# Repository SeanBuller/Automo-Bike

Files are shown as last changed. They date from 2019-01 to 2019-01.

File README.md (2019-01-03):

## Automo-Bike

Automatic bicycle gear changer (transmission). Fourth year design project (Capstone) for ECE (Electrical & Computer Engineering) at University of Waterloo.

## Synopsis

Controls 2 stepper motors based on external inputs from hall-effect sensor, and IMU (inertial measurement unit). 12 V battery input with 5 V regulator for MCU. 

The design is intended to be paired with the following stepper motors: 17HS13-0404S-PG27 and SY20STH30-0604A.

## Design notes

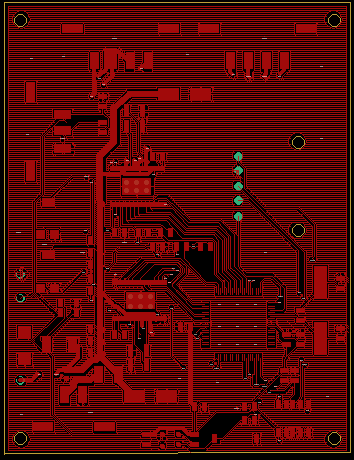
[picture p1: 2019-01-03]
FYDP-Schematic.GTL.png

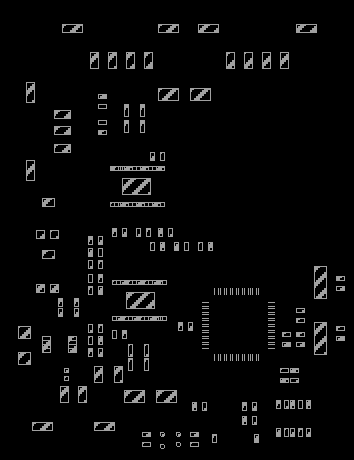
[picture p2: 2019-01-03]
FYDP-Schematic.GTP.png

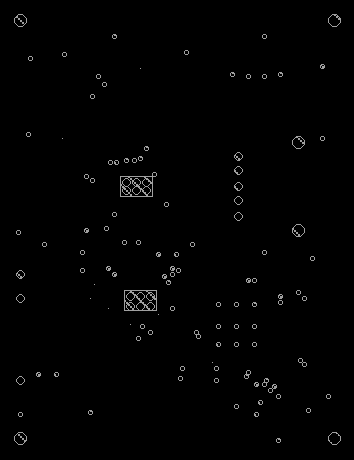
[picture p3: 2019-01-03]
FYDP-Schematic.GBS.png

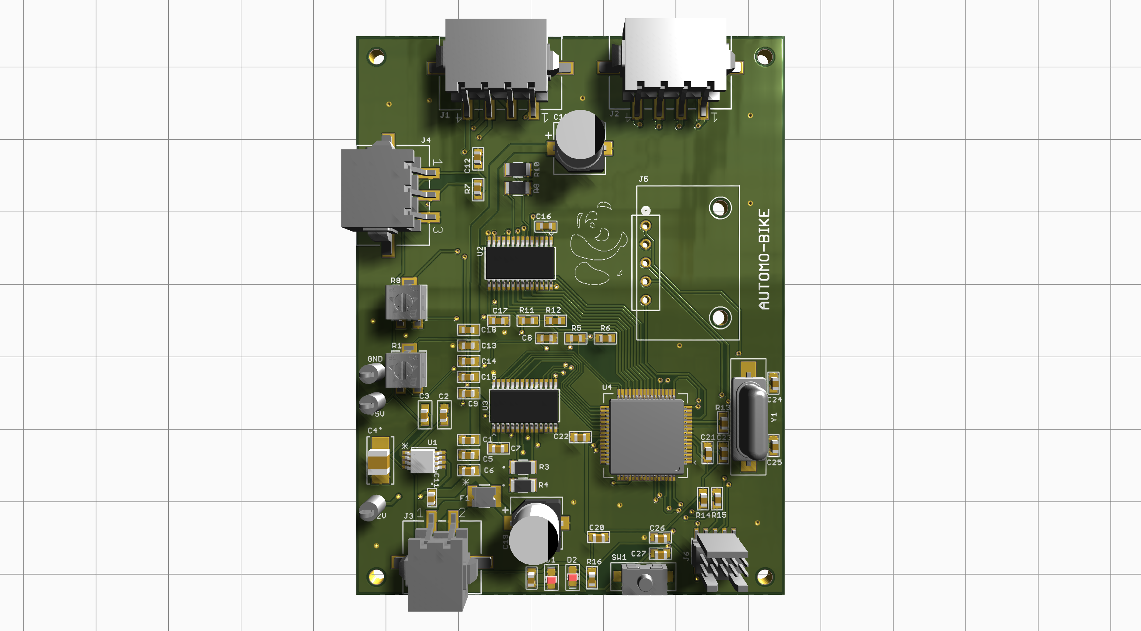
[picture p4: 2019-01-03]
FYDP-Schematic.brd.png

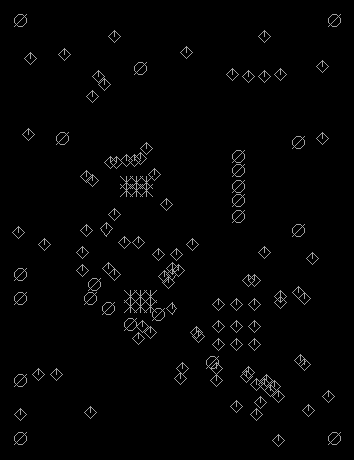
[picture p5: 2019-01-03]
FYDP-Schematic.TXT.png

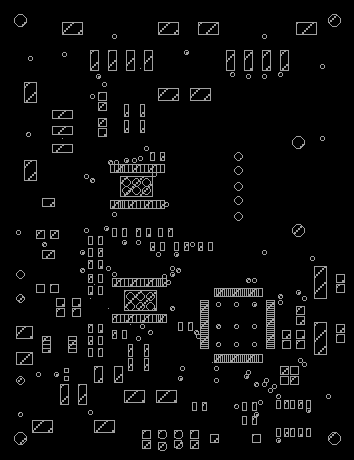
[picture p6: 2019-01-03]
FYDP-Schematic.GTS.png

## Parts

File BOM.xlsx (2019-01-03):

Qty | Value | Device | Package | Parts | Digikey Part # | Unit Price | Per Board Price
11 | 0.1 uF | C_0603 | 603 | C21, C22, C26, C27, C5, C6, C9, C12, C14, C15, C18 | 399-6856-1-ND | $0.13 | $0.82
2 | 0.47uF | C_0603 | 603 | C8, C17 | 490-3295-1-ND | $0.23 | $0.46
2 | 1.0uF | 1.0UF-0603-16V-10% | 603 | C2, C3 | 587-1251-1-ND | $0.13 | $0.26
4 | 1.5K | R_0603 | 603 | R5, R6, R11, R12 | RNCP0603FTD1K50CT-ND | $0.14 | $0.56
2 | 10K | R_0603 | 603 | R14, R15 | RR08P10.0KDCT-ND | $0.16 | $0.32
2 | 10nF | C_0603 | 603 | C7, C16 | 399-1091-1-ND | $0.13 | $0.26
1 | 10uF | F931C106MBA | F93-C | C4 | 478-8238-1-ND | $0.68 | $0.68
1 | 10uF | GRM188C81C106MA73D | G-188 | C11 | 490-7198-1-ND | $0.51 | $0.51
1 | 1210L110/12WR | 1210L110/12WR | 1210LSERIES | F1 | F6132CT-ND | $1.33 | $1.33
2 | 12pF | C_0603 | 603 | C24, C25 | 1276-1254-1-ND | $0.13 | $0.26
1 | 16 MHz | AT-16.000MAGE-T | AT-16.000MAGE-T | Y1 | 887-1608-1-ND | $0.94 | $0.94
3 | 1K | R_0603 | 603 | R2, R7, R16 | RR08P1.0KDCT-ND | $0.16 | $0.48
1 | 1M | R_0603 | 603 | R13 | A119955CT-ND | $0.74 | $0.74
2 | 2.2 uF | C_0603 | 603 | C20, C23 | 587-1430-1-ND | $0.16 | $0.32
1 | 2029030-2 | 2029030-2 | CONN_2029030-2 | J3 | A99181CT-ND | $1.21 | $1.21
1 | 2029030-3 | 2029030-3 | CONN_2029030-3 | J4 | A99182CT-ND | $1.27 | $1.27
2 | 2029030-4 | 2029030-4 | CONN_2029030-4 | J1, J2 | A99183CT-ND | $1.37 | $2.74
2 | 3314G-1-103E | 3314G-1-103E | POT_3314G | R1, R8 | 3314G-103ECT-ND | $3.10 | $6.20
2 | 4.7uF | C_0603 | 603 | C1, C13 | 1276-2087-1-ND | $0.19 | $0.38
1 | 5-535541-3 | 5-535541-3 | 5-535541-3 | J5 | A32919-ND | $1.95 | $1.95
1 | CORTEX_DEBUG_SMD | CORTEX_DEBUG_SMD | SAMTECH_FTSH-105-01 | J6 | SAM8799-ND | $4.18 | $4.18
4 | CSR1206FKR200 | CSR1206FKR200 | STA_CSR1206 | R3, R4, R9, R10 | CSR1206FKR200CT-ND | $0.64 | $2.56
2 | DRV8825PWP | DRV8825PWP | TSSOP-28 | U2, U3 | 296-28915-5-ND | $6.36 | $12.72
1 | RED | LED-RED0603 | LED-0603 | D2 | 160-1447-1-ND | $0.39 | $0.39
1 | GREEN | LED-GREEN0603 | LED-0603 | D1 | 160-1446-1-ND | $0.39 | $0.39
1 | KSR223GNCLFG | KSR223GNCLFG | KSR223GNCLFG | SW1 | 401-1704-1-ND | $1.86 | $1.86
1 | LT3063IMS8E-5#PBF-ND | LT3063IMS8EPBF | MSOP-8_MS | U1 | LT3063IMS8E-5#PBF-ND | $5.57 | $5.57
1 | S9KEA128 | S9KEA128 | S9KEA128 | U4 | S9KEAZ128AMLH-ND | $5.23 | $5.23
1 | TESTPOINT | TESTPOINT | TESTPOINT | GND | 36-5001-ND | $0.53 | $0.53
2 | TESTPOINT | TESTPOINT | TESTPOINT | +5V, +12V | 36-5000-ND | $0.53 | $1.06
2 | UWX1C101MCL1GB | UWX1C101MCL1GB | PCAP_6.3X5.4-ELECT | C10, C19 | 493-2105-1-ND | $0.44 | $0.88
2 | 2029047-4 |  |  |  | A99177-ND | $0.75 | $1.50
1 | 2029047-3 |  |  |  | A99176-ND | $0.65 | $0.65
1 | 2029047-2 |  |  |  | A99175-ND | $0.56 | $0.56
 |  |  |  |  |  | TOTAL | $59.77

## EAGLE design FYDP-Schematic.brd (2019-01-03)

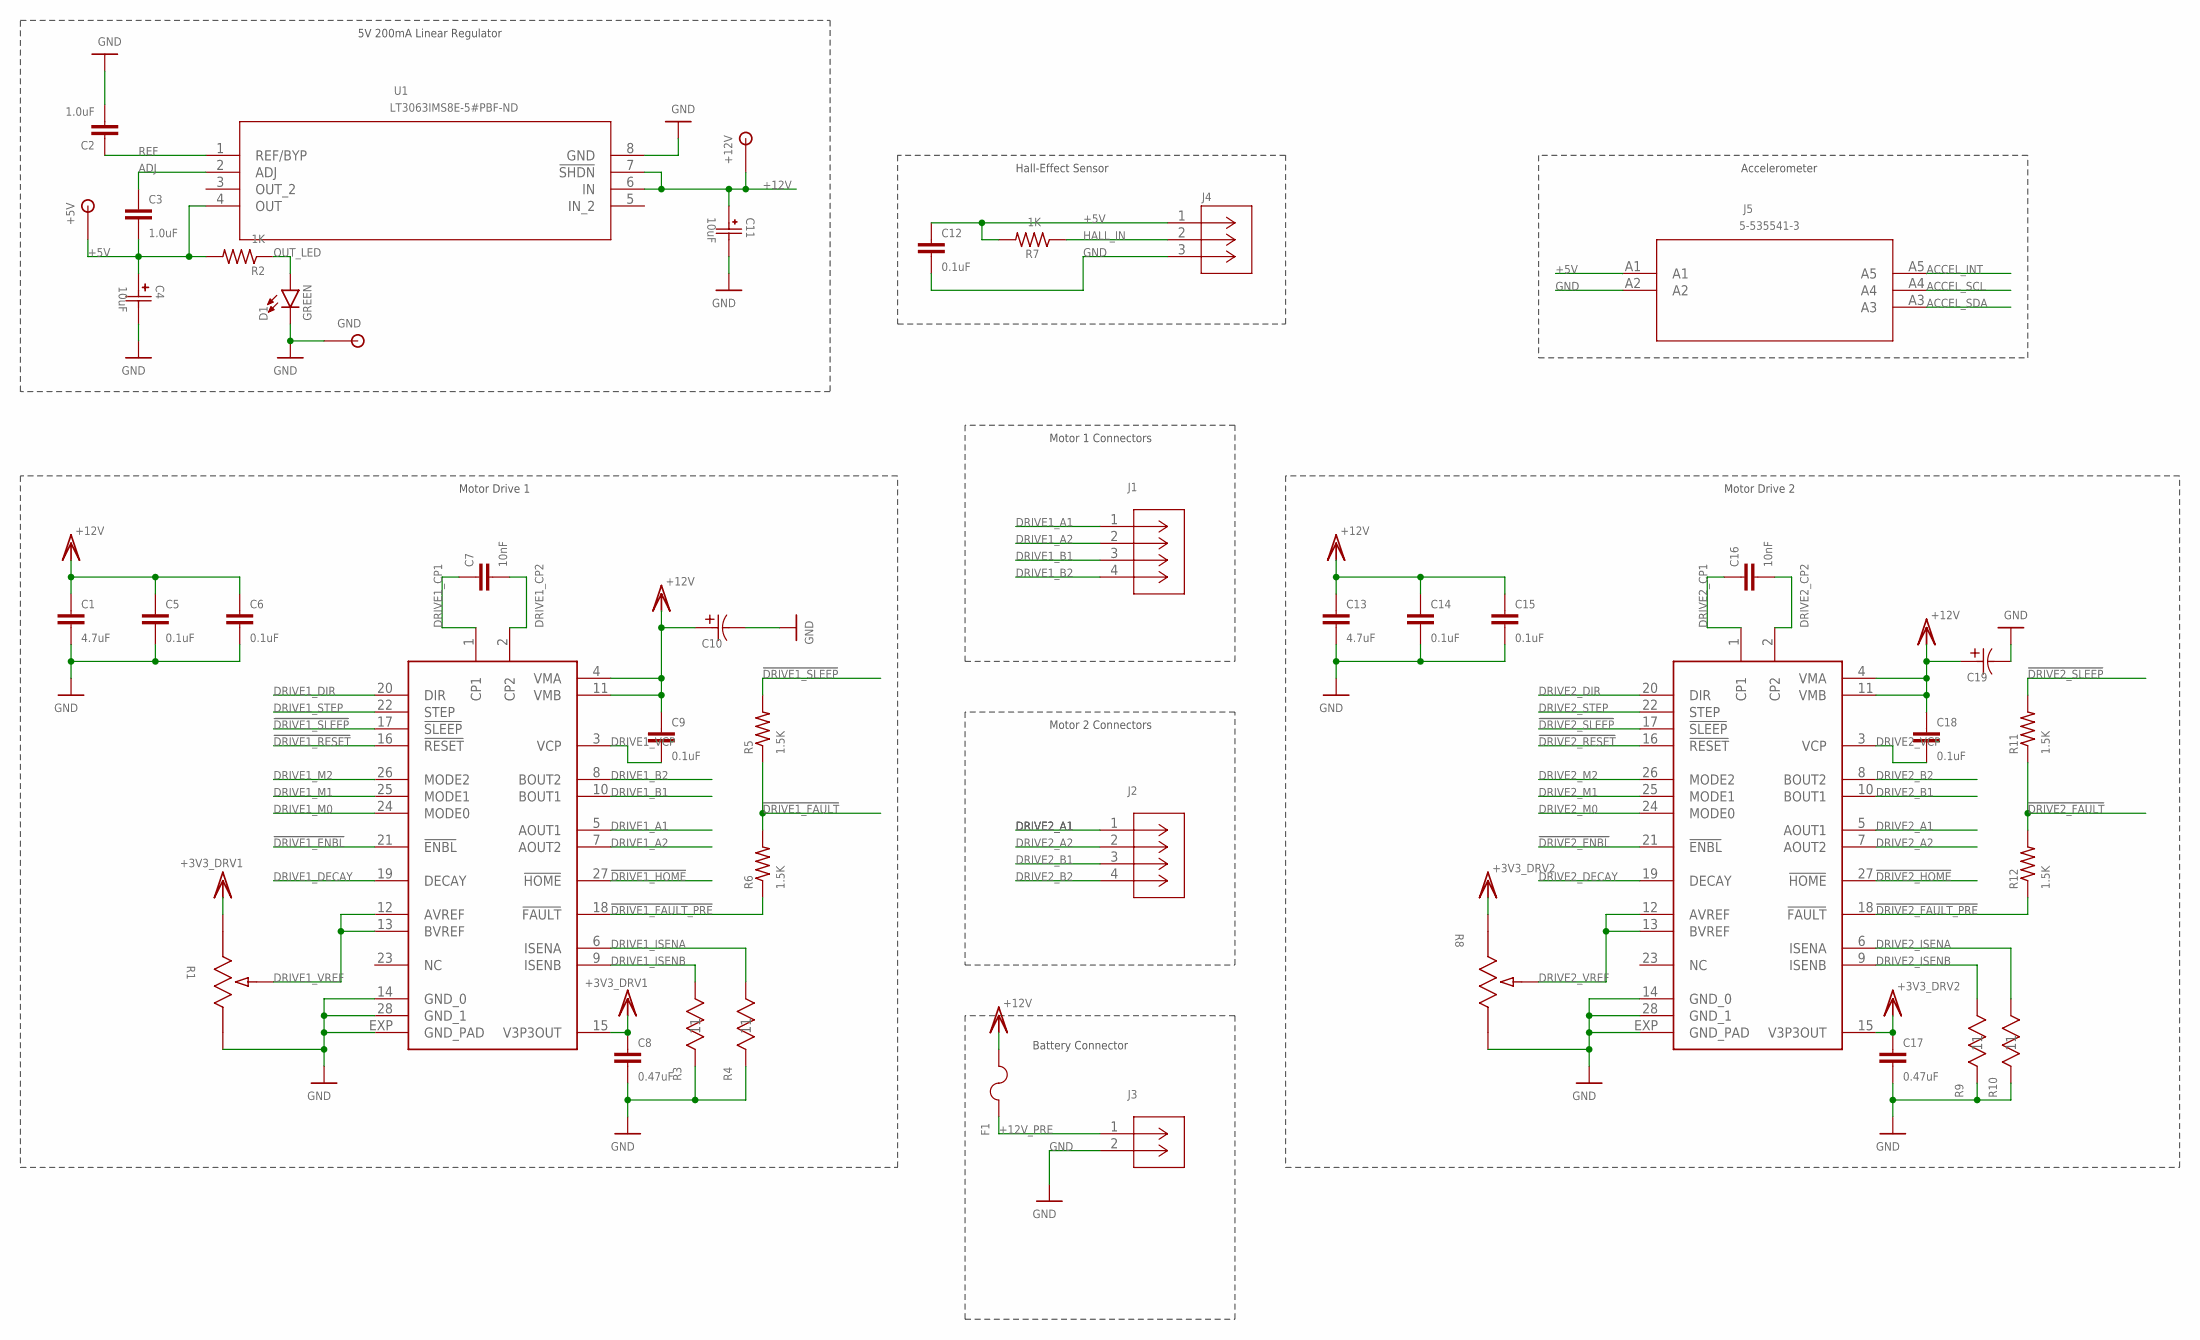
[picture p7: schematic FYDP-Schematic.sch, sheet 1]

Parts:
+5V, +12V: TESTPOINT
C1, C13: 4.7uF; 0603
C2, C3: 1.0uF; 0603
C4: 10uF; F93-C
C5, C6, C9, C12, C14, C15, C18: 0.1uF; 0603
C7, C16: 10nF; 0603
C8, C17: 0.47uF; 0603
C10, C19: UWX1C101MCL1GB; PCAP_6.3X5.4-ELECT
C11: 10uF; G-188
D1: GREEN; LED-0603
F1: 1210L110/12WR; 1210LSERIES
GND: TESTPOINT
J1, J2: 2029030-4; CONN_2029030-4
J3: 2029030-2; CONN_2029030-2
J4: 2029030-3; CONN_2029030-3
J5: 5-535541-3
R1, R8: 3314G-1-103E; POT_3314G
R2, R7: 1K; 0603
R3, R4, R9, R10: CSR1206FKR200; STA_CSR1206
R5, R6, R11, R12: 1.5K; 0603
U1: LT3063IMS8E-5#PBF-ND; MSOP-8_MS
U2, U3: DRV8825PWP; TSSOP-28

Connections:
!DRIVE1_ENBL!: U3.21 (!ENBL!); also elsewhere on the board
!DRIVE1_FAULT!: R5.1, R6.2; also elsewhere on the board
!DRIVE1_FAULT_PRE!: R6.1, U3.18 (!FAULT!)
!DRIVE1_HOME!: U3.27 (!HOME!); also elsewhere on the board
!DRIVE1_RESET!: U3.16 (!RESET!); also elsewhere on the board
!DRIVE1_SLEEP!: R5.2, U3.17 (!SLEEP!); also elsewhere on the board
!DRIVE2_ENBL!: U2.21 (!ENBL!); also elsewhere on the board
!DRIVE2_FAULT!: R11.1, R12.2; also elsewhere on the board
!DRIVE2_FAULT_PRE!: R12.1, U2.18 (!FAULT!)
!DRIVE2_HOME!: U2.27 (!HOME!); also elsewhere on the board
!DRIVE2_RESET!: U2.16 (!RESET!); also elsewhere on the board
!DRIVE2_SLEEP!: R11.2, U2.17 (!SLEEP!); also elsewhere on the board
+3V3_DRV1: C8.1, R1.1, U3.15 (V3P3OUT)
+3V3_DRV2: C17.1, R8.1, U2.15 (V3P3OUT)
+5V: +5V.TP, C3.2, C4.POS (1), C12.1, J4.1, J5.A1, R2.2, R7.2, U1.4 (OUT); also elsewhere on the board
+12V: +12V.TP, C1.1, C5.1, C6.1, C9.1, C10.1 (11), C11.PWR, C13.1, C14.1, C15.1, C18.1, C19.1 (11), F1.2, U1.6 (IN), U1.7 (!SHDN), U2.4 (VMA), U2.11 (VMB), U3.4 (VMA), U3.11 (VMB)
+12V_PRE: F1.1, J3.1
ACCEL_INT: J5.A5; also elsewhere on the board
ACCEL_SCL: J5.A4; also elsewhere on the board
ACCEL_SDA: J5.A3; also elsewhere on the board
ADJ: C3.1, U1.2 (ADJ)
DRIVE1_A1: J1.1, U3.5 (AOUT1)
DRIVE1_A2: J1.2, U3.7 (AOUT2)
DRIVE1_B1: J1.3, U3.10 (BOUT1)
DRIVE1_B2: J1.4, U3.8 (BOUT2)
DRIVE1_CP1: C7.1, U3.1 (CP1)
DRIVE1_CP2: C7.2, U3.2 (CP2)
DRIVE1_DECAY: U3.19 (DECAY); also elsewhere on the board
DRIVE1_DIR: U3.20 (DIR); also elsewhere on the board
DRIVE1_ISENA: R4.2 (22), U3.6 (ISENA)
DRIVE1_ISENB: R3.2 (22), U3.9 (ISENB)
DRIVE1_M0: U3.24 (MODE0); also elsewhere on the board
DRIVE1_M1: U3.25 (MODE1); also elsewhere on the board
DRIVE1_M2: U3.26 (MODE2); also elsewhere on the board
DRIVE1_STEP: U3.22 (STEP); also elsewhere on the board
DRIVE1_VCP: C9.2, U3.3 (VCP)
DRIVE1_VREF: R1.2, U3.12 (AVREF), U3.13 (BVREF)
DRIVE2_A1: J2.1, U2.5 (AOUT1)
DRIVE2_A2: J2.2, U2.7 (AOUT2)
DRIVE2_B1: J2.3, U2.10 (BOUT1)
DRIVE2_B2: J2.4, U2.8 (BOUT2)
DRIVE2_CP1: C16.1, U2.1 (CP1)
DRIVE2_CP2: C16.2, U2.2 (CP2)
DRIVE2_DECAY: U2.19 (DECAY); also elsewhere on the board
DRIVE2_DIR: U2.20 (DIR); also elsewhere on the board
DRIVE2_ISENA: R10.2 (22), U2.6 (ISENA)
DRIVE2_ISENB: R9.2 (22), U2.9 (ISENB)
DRIVE2_M0: U2.24 (MODE0); also elsewhere on the board
DRIVE2_M1: U2.25 (MODE1); also elsewhere on the board
DRIVE2_M2: U2.26 (MODE2); also elsewhere on the board
DRIVE2_STEP: U2.22 (STEP); also elsewhere on the board
DRIVE2_VCP: C18.2, U2.3 (VCP)
DRIVE2_VREF: R8.2, U2.12 (AVREF), U2.13 (BVREF)
GND: C1.2, C2.2, C4.GND (2), C5.2, C6.2, C8.2, C10.2 (22), C11.GND, C12.2, C13.2, C14.2, C15.2, C17.2, C19.2 (22), D1.C, GND.TP, J3.2, J4.3, J5.A2, R1.3, R3.1 (11), R4.1 (11), R8.3, R9.1 (11), R10.1 (11), U1.8 (GND), U2.14 (GND_0), U2.28 (GND_1), U2.EXP (GND_PAD), U3.14 (GND_0), U3.28 (GND_1), U3.EXP (GND_PAD); also elsewhere on the board
HALL_IN: J4.2, R7.1; also elsewhere on the board
OUT_LED: D1.A, R2.1
REF: C2.1, U1.1 (REF/BYP)

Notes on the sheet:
Motor 1 Connectors
Battery Connector
Motor 2 Connectors
5V 200mA Linear Regulator
Motor Drive 1
Motor Drive 2
Hall-Effect Sensor
Accelerometer

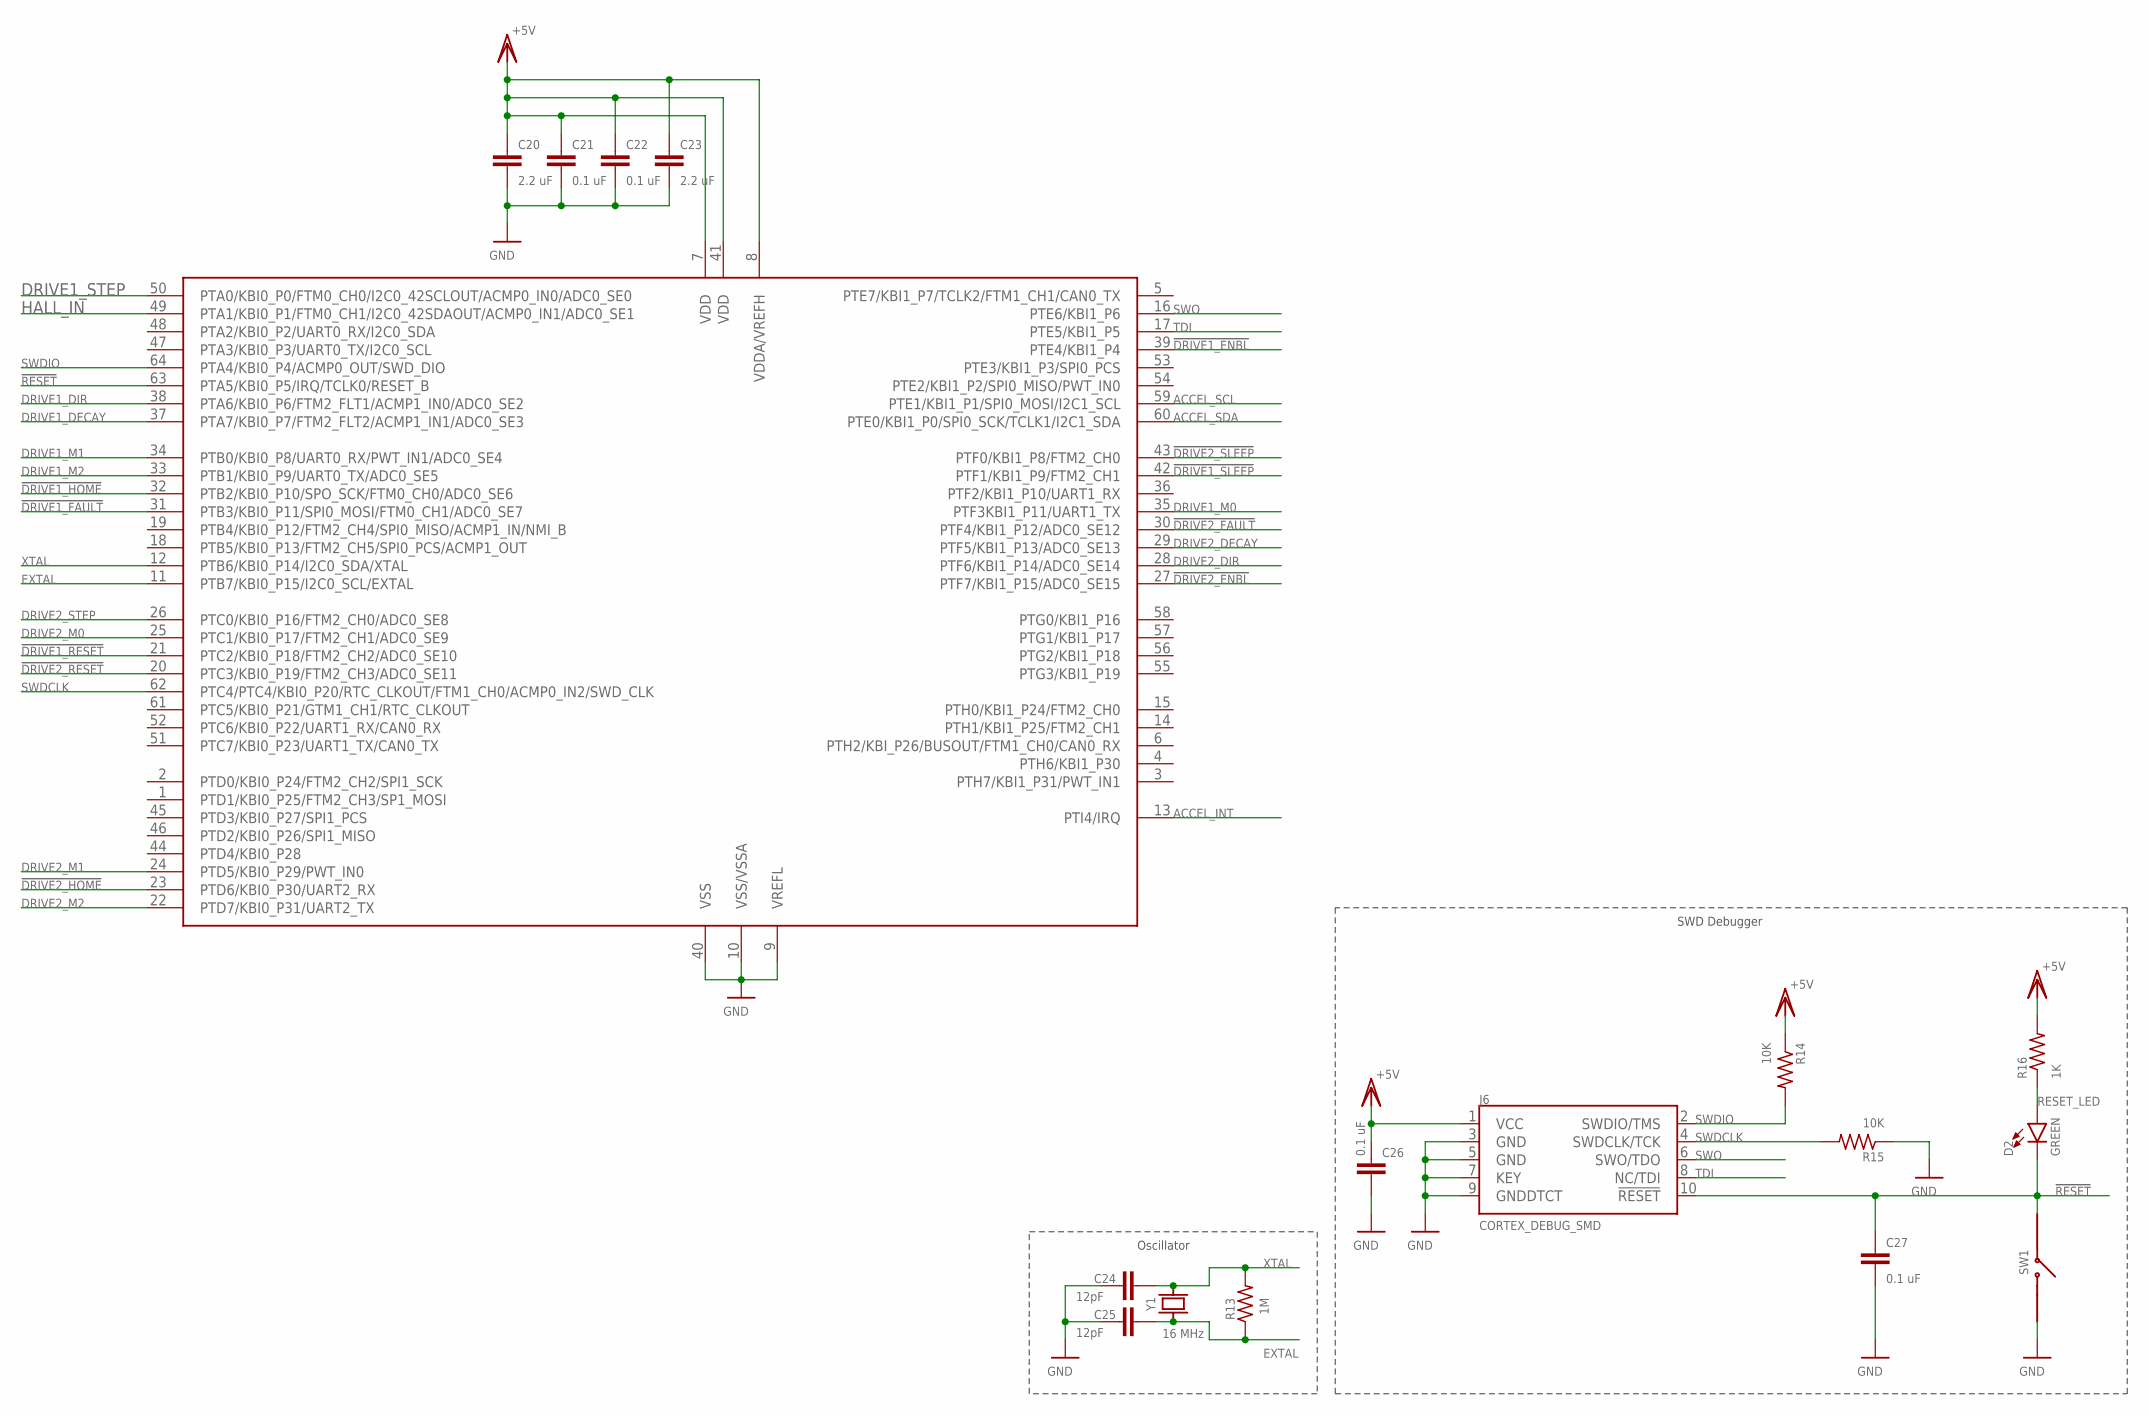
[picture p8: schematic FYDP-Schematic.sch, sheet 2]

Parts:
C20, C23: 2.2 uF; 0603
C21, C22, C26, C27: 0.1 uF; 0603
C24, C25: 12pF; 0603
D2: GREEN; LED-0603
J6: CORTEX_DEBUG_SMD; SAMTECH_FTSH-105-01
R13: 1M; 0603
R14, R15: 10K; 0603
R16: 1K; 0603
SW1: KSR223GNCLFG
U4: S9KEA128
Y1: 16 MHz; AT-16.000MAGE-T

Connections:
!DRIVE1_ENBL!: U4.39 (PTE4/KBI1_P4); also elsewhere on the board
!DRIVE1_FAULT!: U4.31 (PTB3/KBI0_P11/SPI0_MOSI/FTM0_CH1/ADC0_S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); also elsewhere on the board
!DRIVE1_HOME!: U4.32 (PTB2/KBI0_P10/SPO_SCK/FTM0_CH0/ADC0_SE6); also elsewhere on the board
!DRIVE1_RESET!: U4.21 (PTC2/KBI0_P18/FTM2_CH2/ADC0_SE10); also elsewhere on the board
!DRIVE1_SLEEP!: U4.42 (PTF1/KBI1_P9/FTM2_CH1); also elsewhere on the board
!DRIVE2_ENBL!: U4.27 (PTF7/KBI1_P15/ADC0_SE15); also elsewhere on the board
!DRIVE2_FAULT!: U4.30 (PTF4/KBI1_P12/ADC0_SE12); also elsewhere on the board
!DRIVE2_HOME!: U4.23 (PTD6/KBI0_P30/UART2_RX); also elsewhere on the board
!DRIVE2_RESET!: U4.20 (PTC3/KBI0_P19/FTM2_CH3/ADC0_SE11); also elsewhere on the board
!DRIVE2_SLEEP!: U4.43 (PTF0/KBI1_P8/FTM2_CH0); also elsewhere on the board
!RESET!: C27.1, D2.C, J6.10 (!RESET), SW1.1, U4.63 (PTA5/KBI0_P5/IRQ/TCLK0/RESET_B)
+5V: C20.1, C21.1, C22.1, C23.1, C26.1, J6.1 (VCC), R14.1, R16.2, U4.7 (VDD), U4.8 (VDDA/VREFH), U4.41 (VDD); also elsewhere on the board
ACCEL_INT: U4.13 (PTI4/IRQ); also elsewhere on the board
ACCEL_SCL: U4.59 (PTE1/KBI1_P1/SPI0_MOSI/I2C1_SCL); also elsewhere on the board
ACCEL_SDA: U4.60 (PTE0/KBI1_P0/SPI0_SCK/TCLK1/I2C1_SDA); also elsewhere on the board
DRIVE1_DECAY: U4.37 (PTA7/KBI0_P7/FTM2_FLT2/ACMP1_IN1/ADC0_S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); also elsewhere on the board
DRIVE1_DIR: U4.38 (PTA6/KBI0_P6/FTM2_FLT1/ACMP1_IN0/ADC0_S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); also elsewhere on the board
DRIVE1_M0: U4.35 (PTF3KBI1_P11/UART1_TX); also elsewhere on the board
DRIVE1_M1: U4.34 (PTB0/KBI0_P8/UART0_RX/PWT_IN1/ADC0_SE4); also elsewhere on the board
DRIVE1_M2: U4.33 (PTB1/KBI0_P9/UART0_TX/ADC0_SE5); also elsewhere on the board
DRIVE1_STEP: U4.50 (PTA0/KBI0_P0/FTM0_CH0/I2C0_42SCLOUT/ACM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); also elsewhere on the board
DRIVE2_DECAY: U4.29 (PTF5/KBI1_P13/ADC0_SE13); also elsewhere on the board
DRIVE2_DIR: U4.28 (PTF6/KBI1_P14/ADC0_SE14); also elsewhere on the board
DRIVE2_M0: U4.25 (PTC1/KBI0_P17/FTM2_CH1/ADC0_SE9); also elsewhere on the board
DRIVE2_M1: U4.24 (PTD5/KBI0_P29/PWT_IN0); also elsewhere on the board
DRIVE2_M2: U4.22 (PTD7/KBI0_P31/UART2_TX); also elsewhere on the board
DRIVE2_STEP: U4.26 (PTC0/KBI0_P16/FTM2_CH0/ADC0_SE8); also elsewhere on the board
EXTAL: C25.1, R13.1, U4.11 (PTB7/KBI0_P15/I2C0_SCL/EXTAL), Y1.1
GND: C20.2, C21.2, C22.2, C23.2, C24.2, C25.2, C26.2, C27.2, J6.3 (GND), J6.5 (GND), J6.7 (KEY), J6.9 (GNDDTCT), R15.1, SW1.2, U4.9 (VREFL), U4.10 (VSS/VSSA), U4.40 (VSS); also elsewhere on the board
HALL_IN: U4.49 (PTA1/KBI0_P1/FTM0_CH1/I2C0_42SDAOUT/ACM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); also elsewhere on the board
RESET_LED: D2.A, R16.1
SWDCLK: J6.4 (SWDCLK/TCK), R15.2, U4.62 (PTC4/PTC4/KBI0_P20/RTC_CLKOUT/FTM1_CH0/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)
SWDIO: J6.2 (SWDIO/TMS), R14.2, U4.64 (PTA4/KBI0_P4/ACMP0_OUT/SWD_DIO)
SWO: J6.6 (SWO/TDO), U4.16 (PTE6/KBI1_P6)
TDI: J6.8 (NC/TDI), U4.17 (PTE5/KBI1_P5)
XTAL: C24.1, R13.2, U4.12 (PTB6/KBI0_P14/I2C0_SDA/XTAL), Y1.2

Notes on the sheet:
SWD Debugger
Oscillator

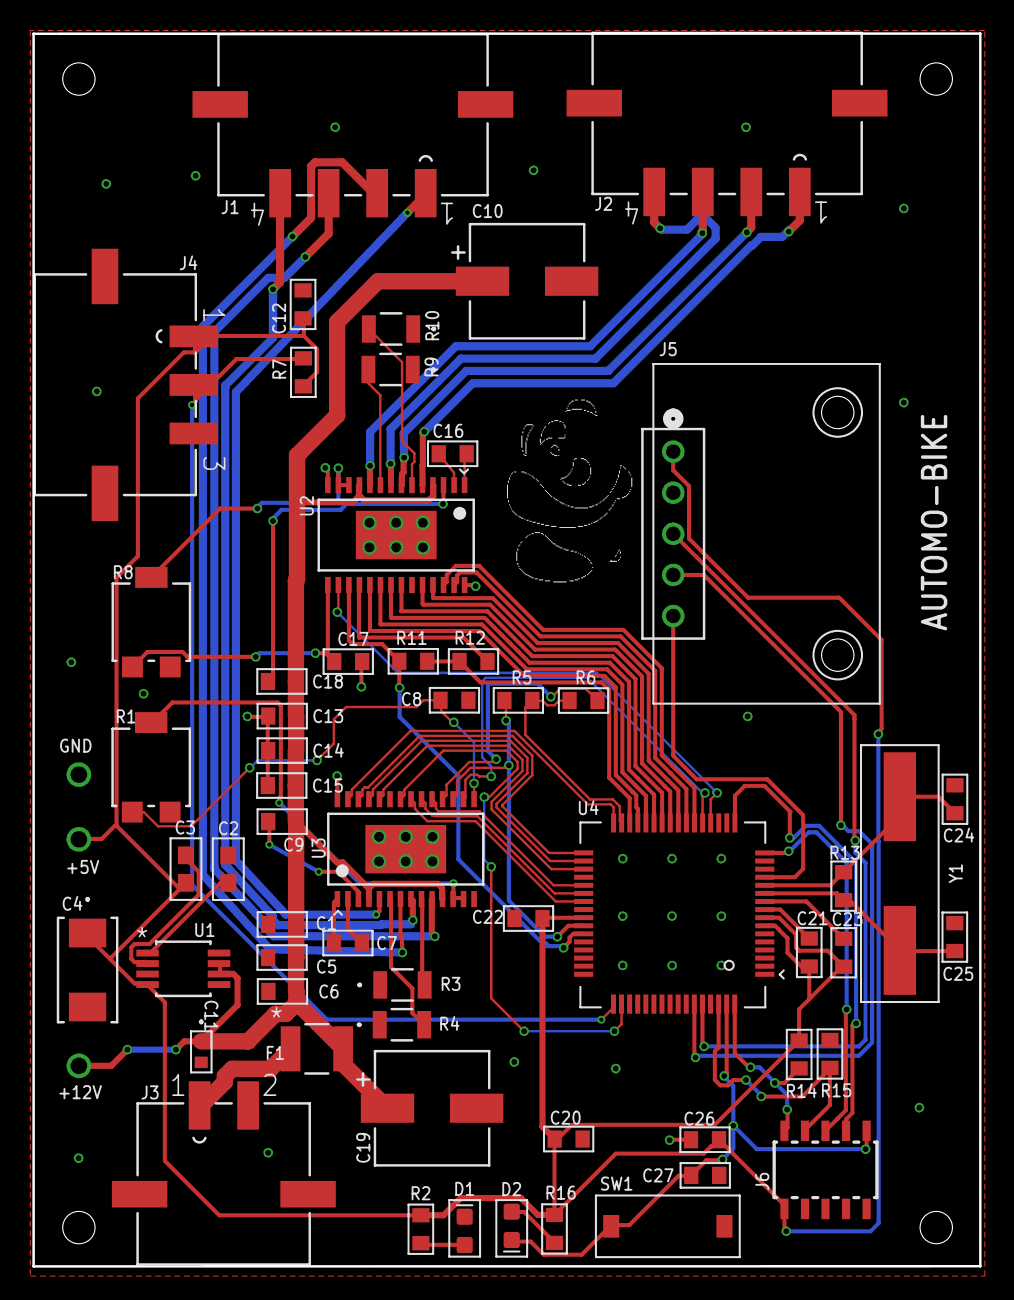
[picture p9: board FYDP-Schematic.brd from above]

Board: 2 copper layers, 58.5 x 76.2 mm, 61 parts (0 on the bottom side), 65 nets.

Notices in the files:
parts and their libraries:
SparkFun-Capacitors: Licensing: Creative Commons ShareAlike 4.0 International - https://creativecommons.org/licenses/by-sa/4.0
